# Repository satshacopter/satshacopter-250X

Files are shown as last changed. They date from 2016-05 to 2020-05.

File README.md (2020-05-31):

<h1 style="font-family: courier;" align="center">satshacopter 250X</h1>
<p align="center">
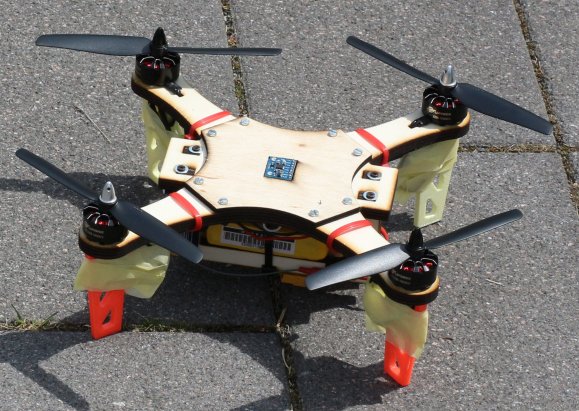
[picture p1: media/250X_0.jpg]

<div align="center"><i>An open source, low cost and fabbable quad X drone.</i></div>
</p>  

satshacopter 250X
--

satshacopter 250X is a quadcopter built around the **[satshakit flight controller](https://github.com/satshakit/satshakit-flight-controller)**. It is designed to be **simple and cheap as much as possible**, and to be easily made inside any **Fab Lab**.

250X specifications:

- **250mm wood frame** and supports
- **open source flight controller**
- **MPU6050 IMU** located exactly at the center
- 4 x 1900kv **brushless motors**
- 4 x 15A **ESCs**
- **MultiWii** compatible
- Hobby King 4 channel **remote and receiver**
- 1000mah 3S **LiPo battery** 
- costs under **100€**

Here you can look about the **MultiWii pin mapping** of the satshakit flight controller board:

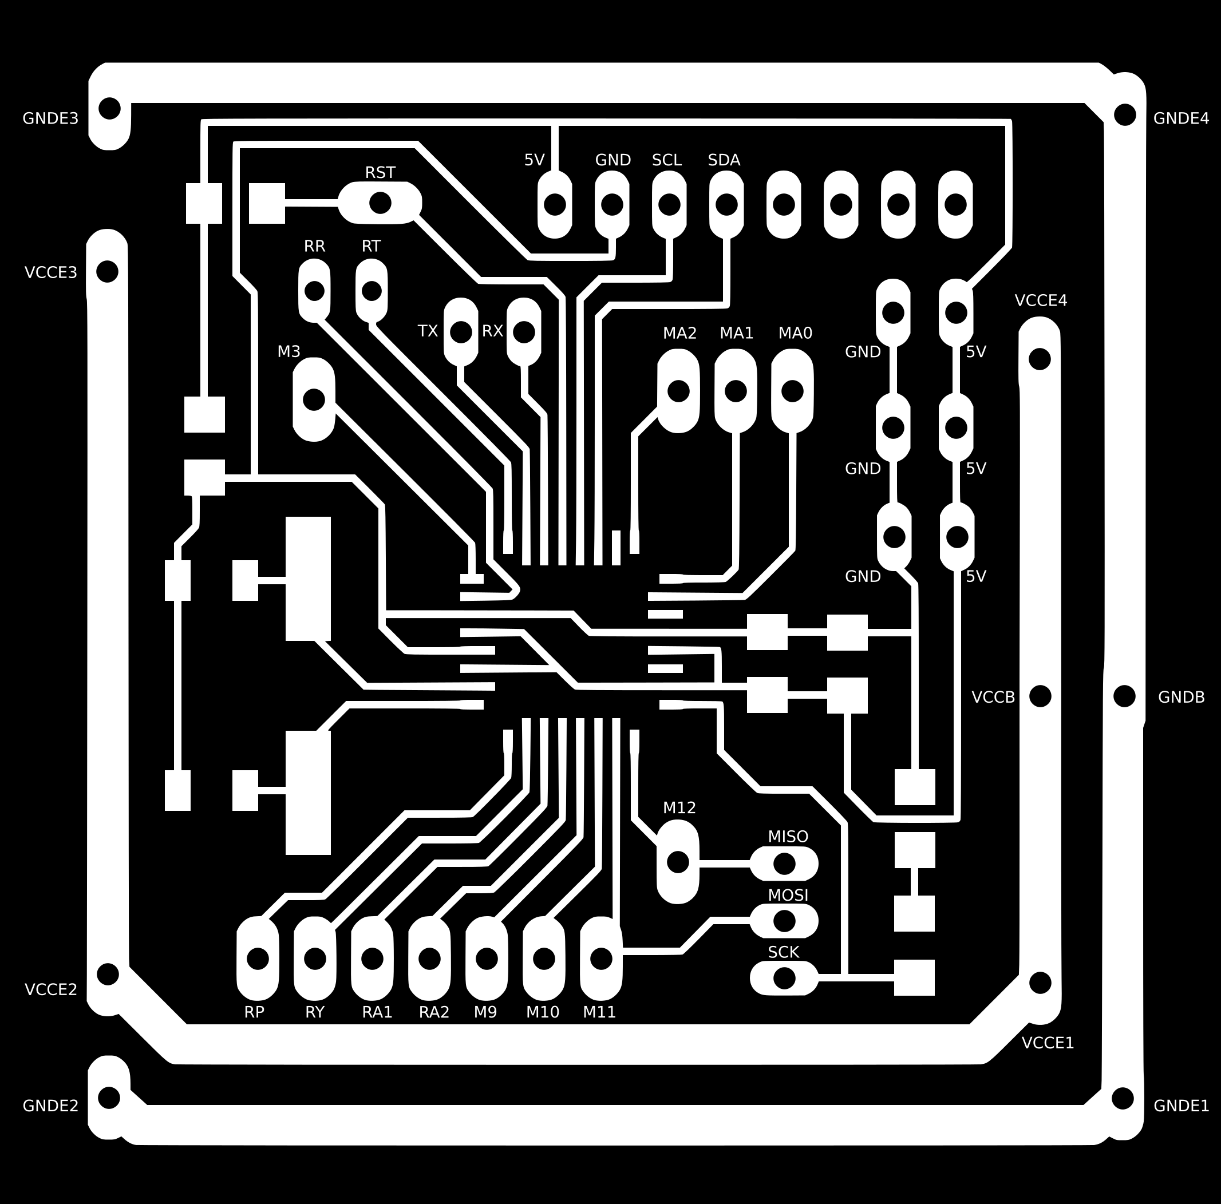
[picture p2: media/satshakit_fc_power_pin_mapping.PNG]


And here you can che the required components in the **Bill of Material** table:

|name|description|vendor|link|price|notes|
|:---:| :---:|:---:|:---:|:---:|:---:|
|2.4Ghz4Ch TxRx V2|4ch mode 2 remote control and receiver|Hobby King|[link](http://www.hobbyking.com/hobbyking/store/__66499__Hobby_King_2_4Ghz_4Ch_Tx_Rx_V2_Mode_2_EU_Warehouse_.html)|23.14€|-|
|Zippy Compact|battery 1000mah 3s|Hobby King|[link](http://www.hobbyking.com/hobbyking/store/__36064__ZIPPY_Compact_1000mAh_3S_25C_Lipo_Pack_EU_Warehouse_.html)|5.55€|-|
|LDPOWER D250-2 Multicopter Power System|4 x 2206-1900kv motors and 4 x 15A ESC|Hobby King EU|[link](http://www.hobbyking.com/hobbyking/store/__84723__LDPOWER_D250_2_Multicopter_Power_System_2206_1900kv_6_x_3_4_Pack_EU_Warehouse_.html)|43.81€|propellers Included|
|IMU 6DOF|MPU6050 Gyro + Acc IMU|Ebay|[link](http://www.ebay.de/itm/MPU-6050-GY-521-3-Achsen-Gyroskop-Accelerometer-Kreisel-Board-Sensor-Arduino-21-/121887579651)|5.39€|-|
|LiPo Charger and Balancer|800mah 3s LiPo charger|Hobby King|[link](http://www.hobbyking.com/hobbyking/store/uh_viewitem.asp?idproduct=77525)|6.99€|-|
|Fligh Controller|satshakit flight controller|various|[link](https://github.com/satshakit/satshakit-flight-controller)|4.00-8.00€|depending on the quantity|
|Voltage regulator|Pololu step up step down 5V S7V7F5|E-shop|[link](https://www.flikto.de/products/pololu-5v-step-up-step-down-voltage-regulator-s7vf5)|4.31€|-|
||||**Total price**|89.19€+4/8€|-|

NOTE: prices may change over time on the respective vendors, and also it is highly dependand on the quantity of drones you want to make.

Downloads
--

If you want to build by yourself a satshacopter 250X, please download the detailed **build manual** here:

- [satshacopter 250X detailed build manual](https://github.com/satshacopter/satshacopter-250X/raw/master/docs/250X/satshacopter-250x-building-manual.pdf)

Following you can find all the **design files** you need to make it:

- [satshakit flight controller eagle board](https://raw.githubusercontent.com/satshacopter/satshacopter-250X/master/eagle_projects/satshakit_flight_controller/satshakit_fc_power.brd)
- [satshakit flight controller eagle sch](https://raw.githubusercontent.com/satshacopter/satshacopter-250X/master/eagle_projects/satshakit_flight_controller/satshakit_fc_power.sch)
- [satshakit flight controller internal traces png](https://raw.githubusercontent.com/satshacopter/satshacopter-250X/master/media/satshakit_fc_power_internal.png)
- [satshakit flight controller holes png](https://raw.githubusercontent.com/satshacopter/satshacopter-250X/master/media/satshakit_fc_power_holes.png)
- [satshakit flight controller cut png](https://raw.githubusercontent.com/satshacopter/satshacopter-250X/master/media/satshakit_fc_power_cut.png)
- [main frame and supports Rhino](https://github.com/satshacopter/satshacopter-250X/raw/master/design_files/main_frame_and_supports_8mm.3dm)
- [main frame and supports dxf](https://github.com/satshacopter/satshacopter-250X/raw/master/design_files/main_frame_and_supports_8mm.dxf)
- [upper frame and supports Rhino](https://github.com/satshacopter/satshacopter-250X/raw/master/design_files/upper_frame_4mm.3dm)
- [upper frame and supports dxf](https://raw.githubusercontent.com/satshacopter/satshacopter-250X/master/design_files/upper_frame_4mm.dxf)
- [foot Rhino](https://github.com/satshacopter/satshacopter-250X/raw/master/design_files/foot.3dm)
- [foot stl](https://github.com/satshacopter/satshacopter-250X/raw/master/design_files/foot.stl)
- [satshacopter 250X detailed BOM Excel](https://github.com/satshacopter/satshacopter-250X/raw/master/docs/250X/250X_BOM.xlsx)
- [satshacopter 250X detailed BOM Open document](https://github.com/satshacopter/satshacopter-250X/raw/master/docs/250X/250_BOM.ods)

Media
--

Some images of a built satshacopter 250X

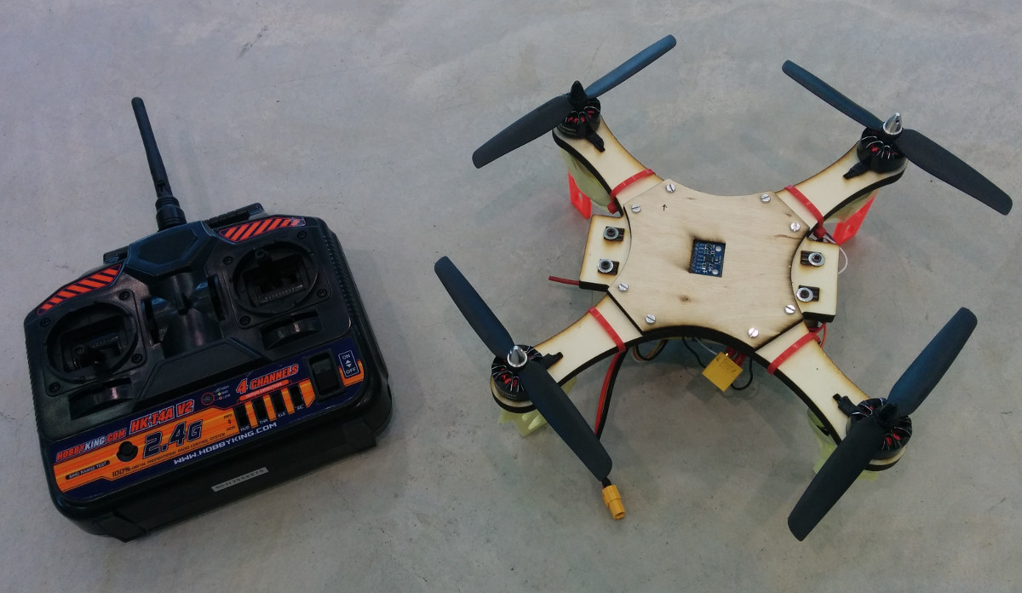
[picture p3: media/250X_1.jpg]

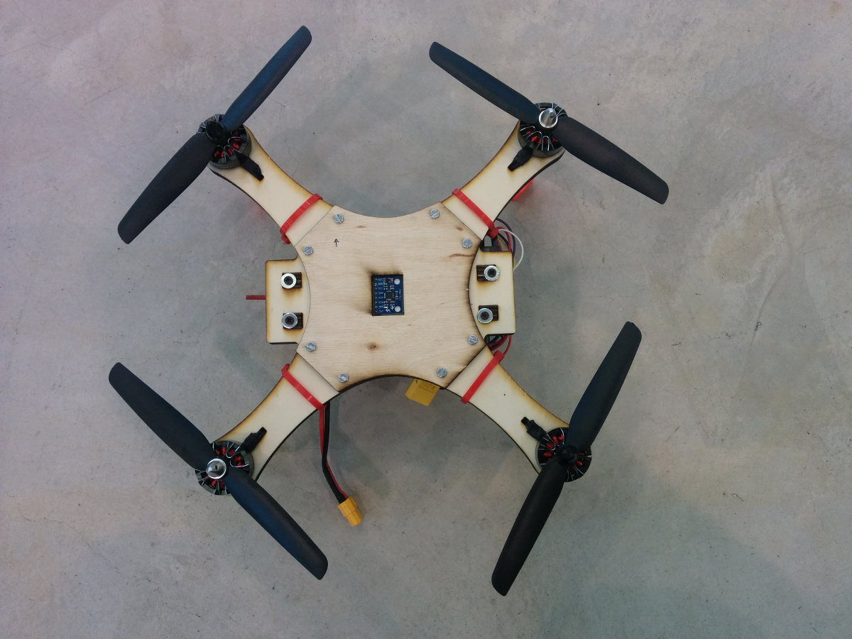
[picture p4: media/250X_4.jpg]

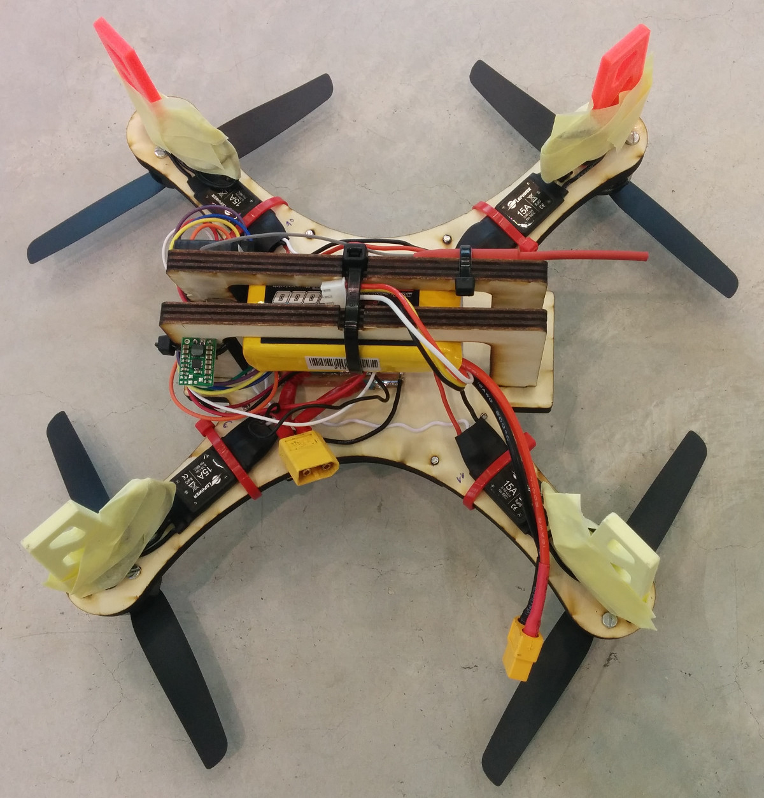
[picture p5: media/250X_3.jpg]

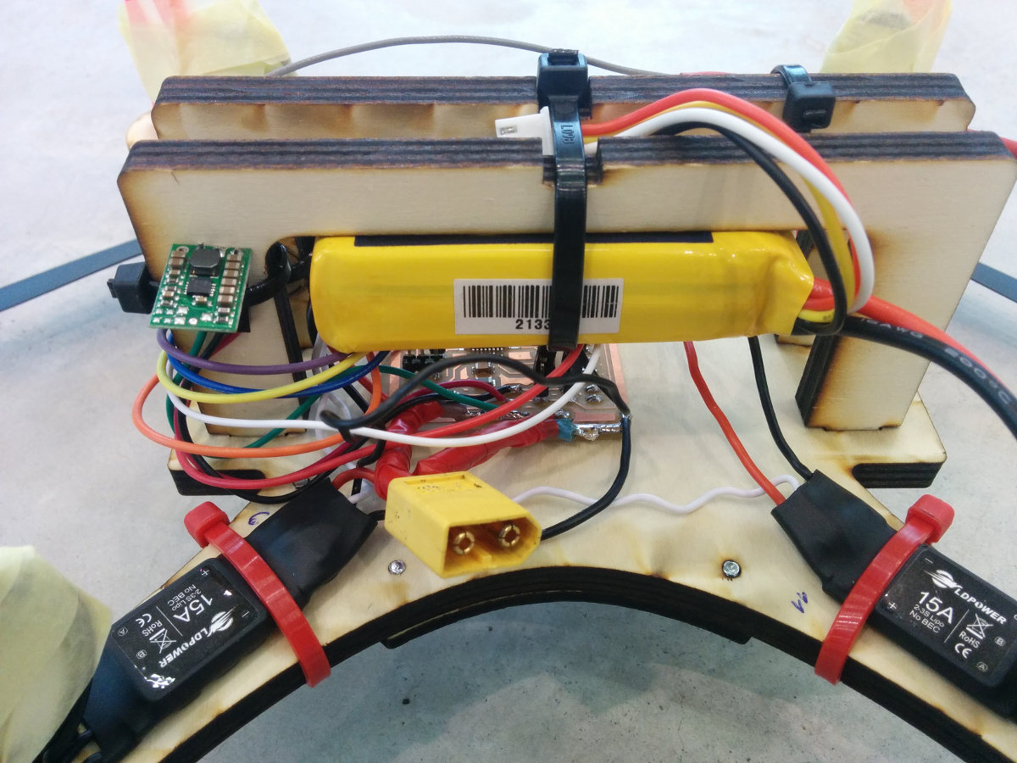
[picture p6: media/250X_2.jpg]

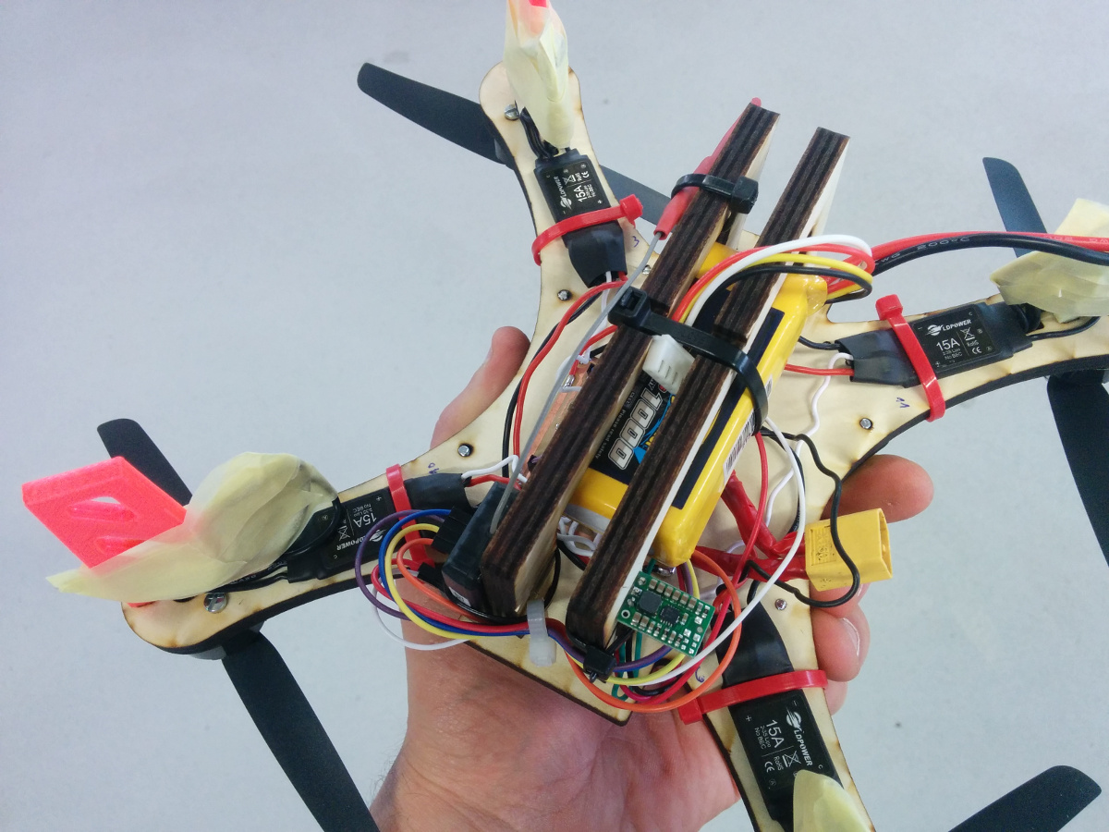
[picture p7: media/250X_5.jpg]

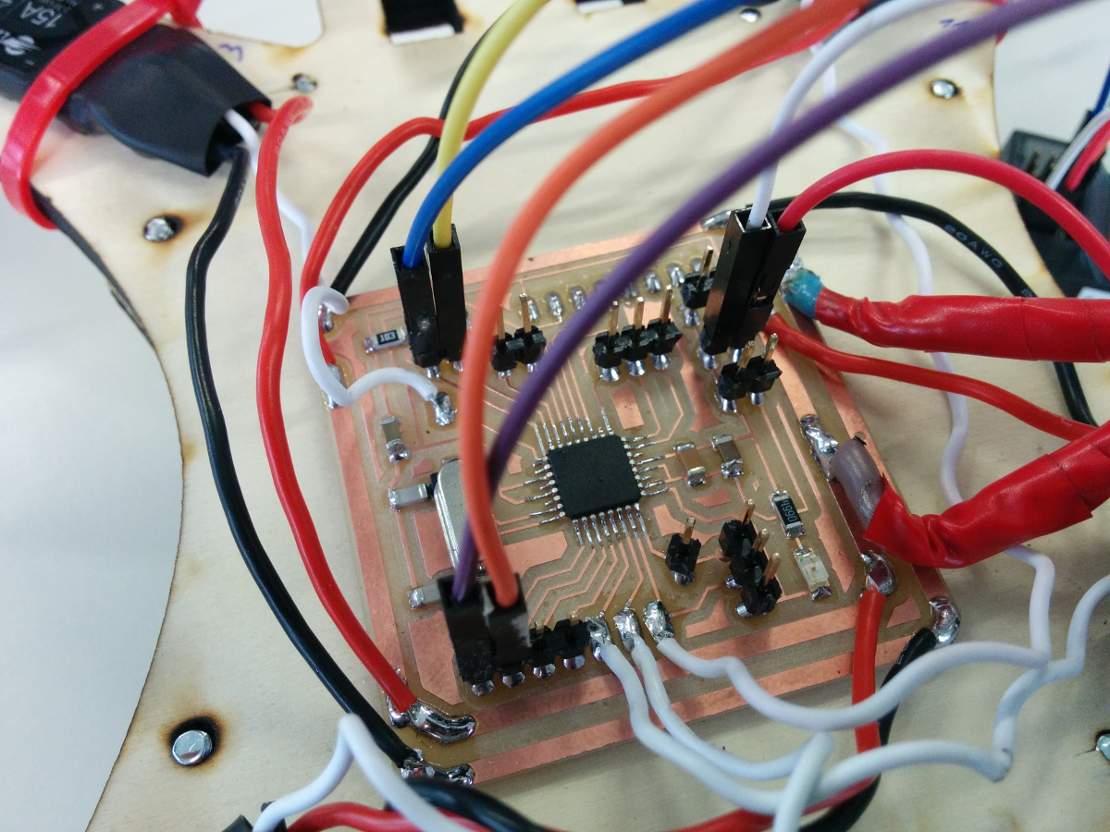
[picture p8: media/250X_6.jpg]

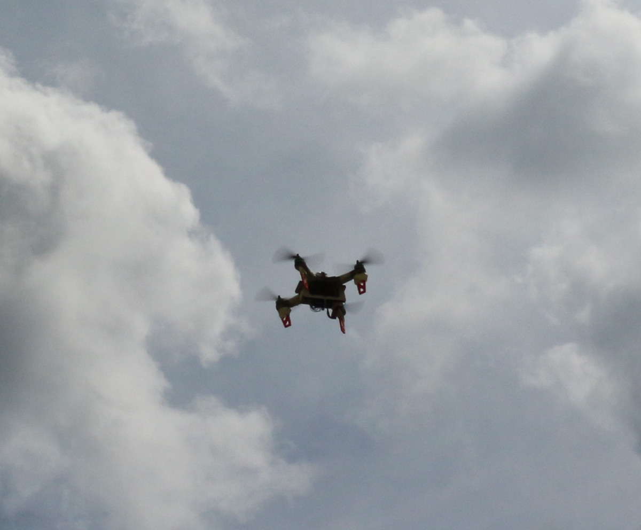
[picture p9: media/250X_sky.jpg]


satshacopter 250X perfomance test:

<a href="http://www.youtube.com/watch?feature=player_embedded&v=MrtPuotW08c
" target="_blank"></a>

Safety
--

Please try always to fly safe.

Here are my personal safety recommendations, especially for experimental drones of which you are not sure on how they can behave:

- make sure to always keep an HUGE distance between you and the drone
- always place yourself on the back of the drone before starting flying
- always have the direct sight to the drone and make sure that its orientation is clear for you (use different colors or LEDs)
- fly in private areas where no public can access
- make sure that nobody can come near the drone while you are flying
- make sure that you cannot destroy anything that you have around you with the drone
- check the wind and the weather before flying, if outdoor
- never go too high (no more than 1/2 meters in these cases)
- do not fly on top of someone (neither yourself)
- first try to fly few cm above the ground to see if everything is correct
- try to avoid using carbon fiber props (they are really like rotating knifes) but use plastic props
- try to use smaller drones with smaller props for really experimental tests
- triple check all the screws and that the frame is not cracked somewhere
- triple check all the DIY electronics, if it fails in-flight can be extremely dangerous
- make sure that the batteries are full charged (both transmitter and the LiPos)

Authors
--

- Daniele Ingrassia

Contact
--

- **ingrassiada@gmail.com**
- **[linkedin](http://it.linkedin.com/in/danieleingrassia)**

Thanks
--

[Fablab Kamp-Lintfort](http://fablab.hochschule-rhein-waal.de/index.php/de/)<br />
Hochschule Rhein-Waal<br />
Friedrich-Heinrich-Allee 25, 47475 Kamp-Lintfort, Germany<br />
fablab@hochschule-rhein-waal.de

License
--
This work is licensed under the terms of the open source license: Creative Commons Attribution-ShareAlike 4.0 International ([CC BY-SA 4.0](https://creativecommons.org/licenses/by-sa/4.0/)).

Disclaimer  
--

<div class="align-justify">
This hardware/software is provided "as is", and you use the hardware/software at your own risk. Under no circumstances shall any author be liable for direct, indirect, special, incidental, or consequential damages resulting from the use, misuse, or inability to use this hardware/software, even if the authors have been advised of the possibility of such damages.</div>

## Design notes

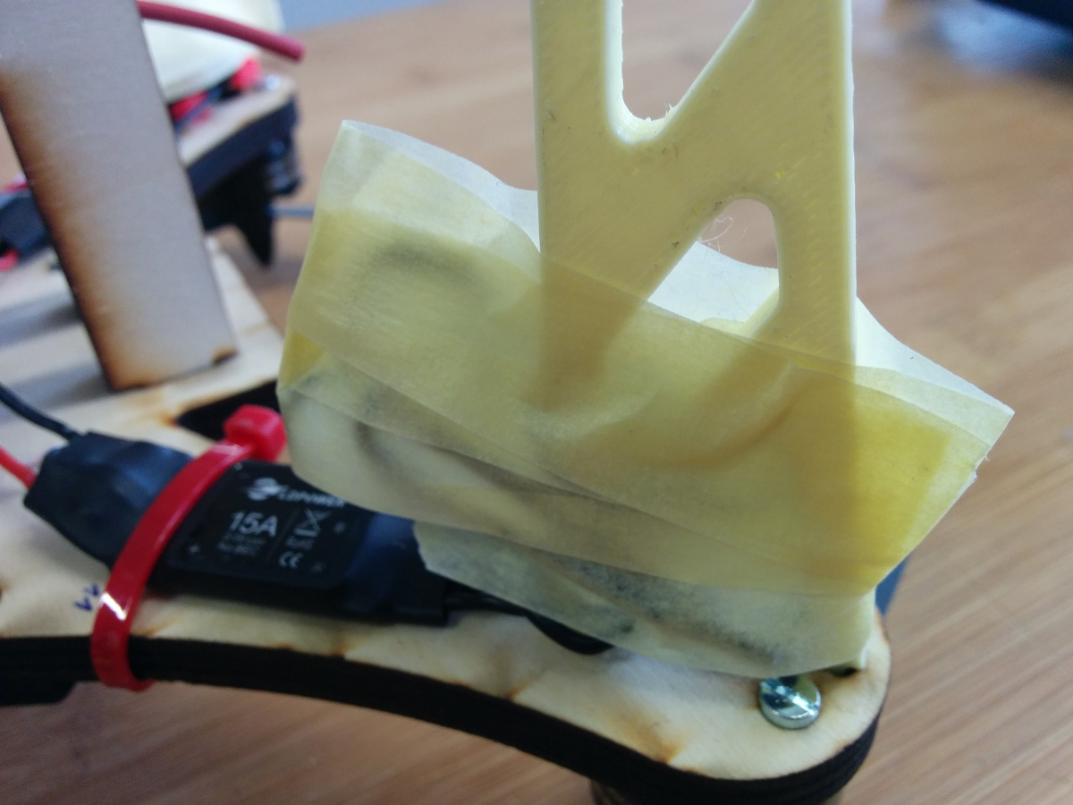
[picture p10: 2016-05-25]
media/scotch_tape_motors.jpg

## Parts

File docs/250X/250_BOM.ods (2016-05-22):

Name | Description | Vendor | Link | Unit Price | Total price x 5 | Notes
2.4Ghz4Ch TxRx V2 | 4ch mode 2 remote control and receiver | Hobby King EU | link (http://www.hobbyking.com/hobbyking/store/__66499__Hobby_King_2_4Ghz_4Ch_Tx_Rx_V2_Mode_2_EU_Warehouse_.html) | 23.14 | 115.70 | -
Zippy Compact | battery 1000mah 3s | Hobby King EU | link (http://www.hobbyking.com/hobbyking/store/__36064__ZIPPY_Compact_1000mAh_3S_25C_Lipo_Pack_EU_Warehouse_.html) | 5.55 | 27.75 | -
LDPOWER D250-2 Multicopter Power System | 4 x 2206-1900kv motors and 4 x 15A esc | Hobby King EU | link (http://www.hobbyking.com/hobbyking/store/__84723__LDPOWER_D250_2_Multicopter_Power_System_2206_1900kv_6_x_3_4_Pack_EU_Warehouse_.html) | 43.81 | 219.05 | Propellers Included
IMU 6DOF | MPU6050 Gyro + Acc IMU | Ebay (local) | link (http://www.ebay.de/itm/MPU-6050-GY-521-3-Achsen-Gyroskop-Accelerometer-Kreisel-Board-Sensor-Arduino-21-/121887579651) | 5.39 | 26.95 | Local (near Rheinberg)
LiPo Charger and Balancer | 800mah 3s LiPo charger | Hobby King EU | link (http://www.hobbyking.com/hobbyking/store/uh_viewitem.asp?idproduct=77525) | 6.99 | 34.95
Frame | 8mm + 2mm plywood frame | Local | - | 2.00 | 10.00 | -
Fligh Controller | satshakit flight controller | Various | - | 4.00 | 20.00
Copper sheet | FR4 80 x 160 | Various | - | 1.00 | 5.00 | A lot of spare space for mistakes in engraving
Battery connectors | XT 60 female connectors | Hobby King EU | link (http://www.hobbyking.com/hobbyking/store/__36304__Female_XT60_Connectors_5pcs_bag_GENUINE_EU_Warehouse_.html) | 0.58 | 2.90 | already x 5
Motor And Frame Screws | M3 10 x 8 + M3 12 x 4 + nuts and washers | Local | - | 0.50 | 2.50 | -
AA Batteries for the remote | 8 x AA 1.5V batteries | Local | - | 1.60 | 8.00 | -
Voltage regulator 5V | S7V7F5 | E-shop | link (https://www.flikto.de/products/pololu-5v-step-up-step-down-voltage-regulator-s7vf5) | 4.31 | 21.55
 |  |  |  | Shipping of all: | 9.00 | 7€ combined Hobby King + 2€ E-shop
 |  |  |  | Price singe drone without shipping | Price 5 drones incl. shipping
 |  |  |  | 98.87 | 503.35

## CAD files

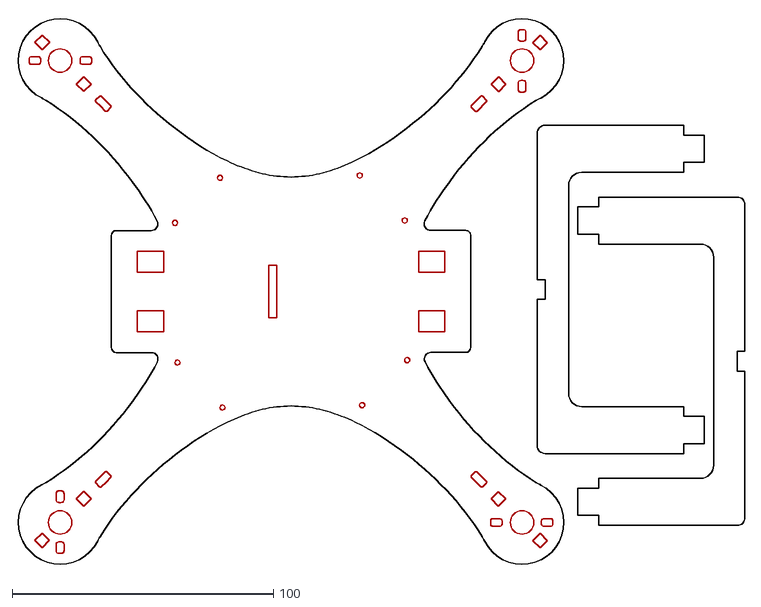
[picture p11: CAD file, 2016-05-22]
design_files/main_frame_and_supports_8mm.dxf
279.0 x 210.5

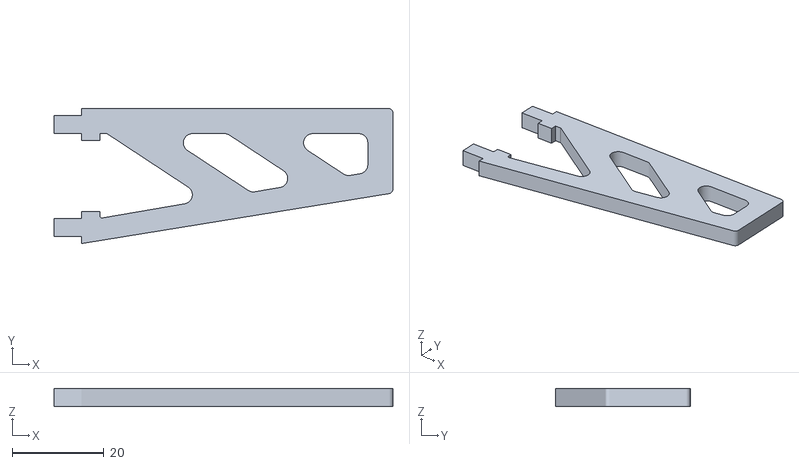
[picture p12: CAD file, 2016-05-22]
design_files/foot.stl
74.0 x 29.5 x 4.00

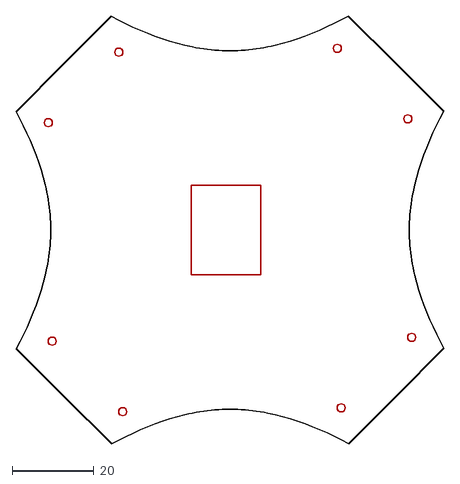
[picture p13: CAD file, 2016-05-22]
design_files/upper_frame_4mm.dxf
104.7 x 104.7

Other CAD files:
design_files/foot.3dm
design_files/main_frame_and_supports_8mm.3dm
design_files/upper_frame_4mm.3dm

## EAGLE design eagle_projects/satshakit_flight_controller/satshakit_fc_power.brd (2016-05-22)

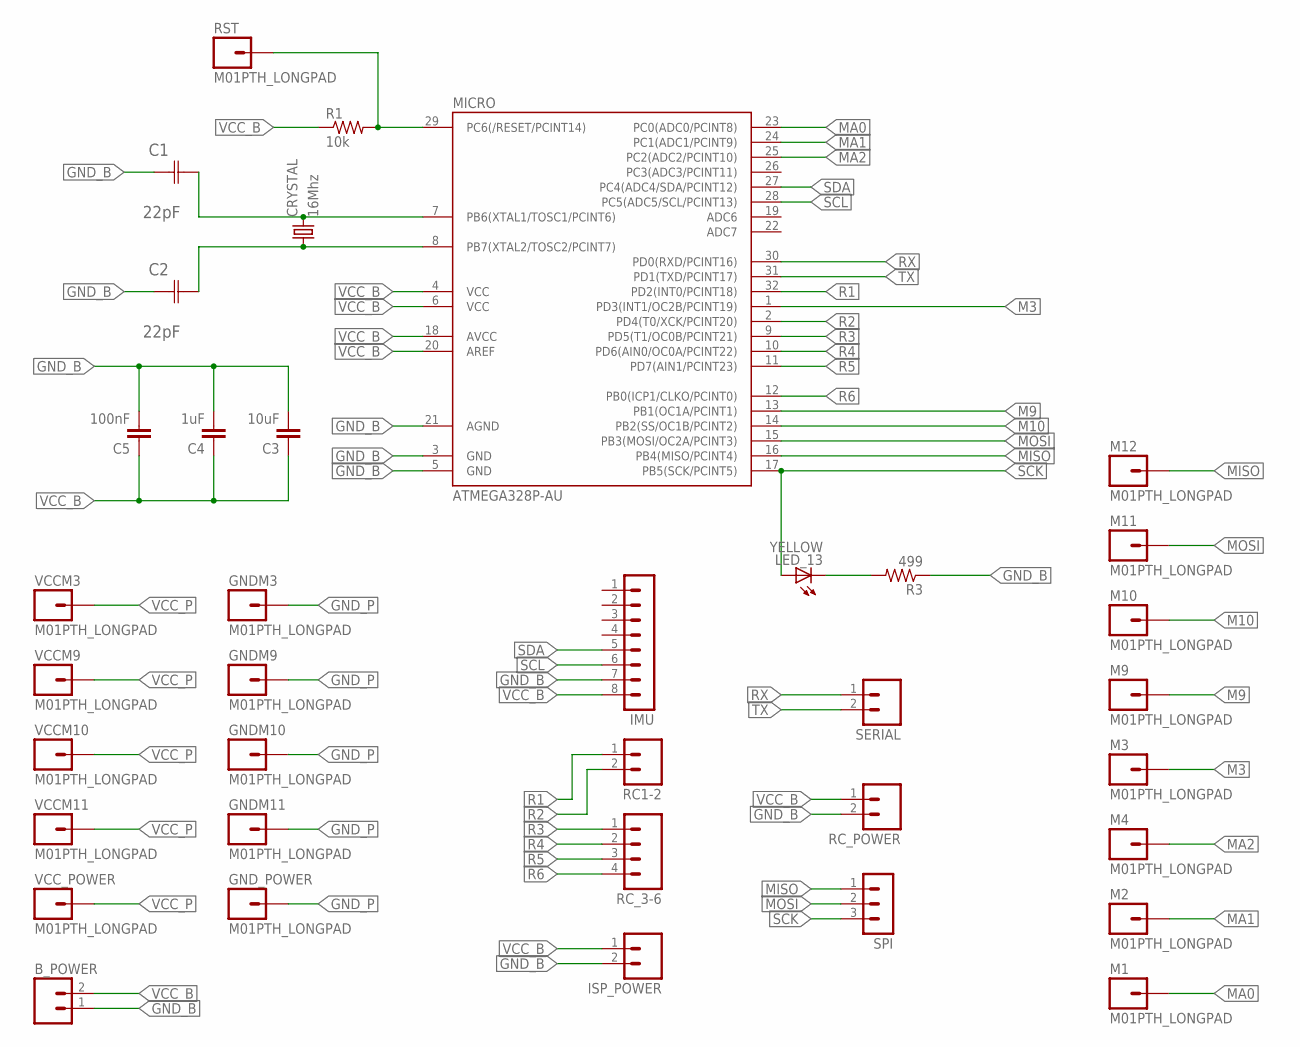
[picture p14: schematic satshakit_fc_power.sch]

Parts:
B_POWER: M02LOCK_LONGPADS; 1X02_LOCK_LONGPADS
C1, C2: 22pF; CAPC3216X178N
C3: 10uF; 1206
C4: 1uF; 1206
C5: 100nF; 1206
CRYSTAL: 16Mhz; CSM-7X-DU
GNDM3, GNDM9, GNDM10, GNDM11: M01PTH_LONGPAD; 1X01_LONGPAD
GND_POWER: M01PTH_LONGPAD; 1X01_LONGPAD
IMU: MA08-1
ISP_POWER: M02LOCK_LONGPADS; 1X02_LOCK_LONGPADS
LED_13: YELLOW; 1206
M1, M2, M3, M4, M9, M10, M11, M12: M01PTH_LONGPAD; 1X01_LONGPAD
MICRO: ATMEGA328P-AU; TQFP32-08
R1: 10k; 1206
R3: 499; 1206
RC1-2: M02; 02P
RC_3-6: M04LONGPADS; 1X04_LONGPADS
RC_POWER: M02LOCK_LONGPADS; 1X02_LOCK_LONGPADS
RST: M01PTH_LONGPAD; 1X01_LONGPAD
SERIAL: M02LOCK_LONGPADS; 1X02_LOCK_LONGPADS
SPI: MA03-1
VCCM3, VCCM9, VCCM10, VCCM11: M01PTH_LONGPAD; 1X01_LONGPAD
VCC_POWER: M01PTH_LONGPAD; 1X01_LONGPAD

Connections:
GND_B: B_POWER.1, C1.1 (C1), C2.1 (C1), C3.2, C4.2, C5.2, IMU.7, ISP_POWER.2, MICRO.3 (GND), MICRO.5 (GND), MICRO.21 (AGND), R3.1, RC_POWER.2
GND_P: GNDM3.1, GNDM9.1, GNDM10.1, GNDM11.1, GND_POWER.1
M3: M3.1, MICRO.1 (PD3(INT1/OC2B/PCINT19))
M9: M9.1, MICRO.13 (PB1(OC1A/PCINT1))
M10: M10.1, MICRO.14 (PB2(SS/OC1B/PCINT2))
MA0: M1.1, MICRO.23 (PC0(ADC0/PCINT8))
MA1: M2.1, MICRO.24 (PC1(ADC1/PCINT9))
MA2: M4.1, MICRO.25 (PC2(ADC2/PCINT10))
MISO: M12.1, MICRO.16 (PB4(MISO/PCINT4)), SPI.1
MOSI: M11.1, MICRO.15 (PB3(MOSI/OC2A/PCINT3)), SPI.2
unnamed: C1.2 (C2), CRYSTAL.2, MICRO.7 (PB6(XTAL1/TOSC1/PCINT6))
unnamed: MICRO.29 (PC6(/RESET/PCINT14)), R1.2, RST.1
unnamed: C2.2 (C2), CRYSTAL.1, MICRO.8 (PB7(XTAL2/TOSC2/PCINT7))
unnamed: LED_13.2 (C), R3.2
R1: MICRO.32 (PD2(INT0/PCINT18)), RC1-2.1
R2: MICRO.2 (PD4(T0/XCK/PCINT20)), RC1-2.2
R3: MICRO.9 (PD5(T1/OC0B/PCINT21)), RC_3-6.1
R4: MICRO.10 (PD6(AIN0/OC0A/PCINT22)), RC_3-6.2
R5: MICRO.11 (PD7(AIN1/PCINT23)), RC_3-6.3
R6: MICRO.12 (PB0(ICP1/CLKO/PCINT0)), RC_3-6.4
RX: MICRO.30 (PD0(RXD/PCINT16)), SERIAL.1
SCK: LED_13.1 (A), MICRO.17 (PB5(SCK/PCINT5)), SPI.3
SCL: IMU.6, MICRO.28 (PC5(ADC5/SCL/PCINT13))
SDA: IMU.5, MICRO.27 (PC4(ADC4/SDA/PCINT12))
TX: MICRO.31 (PD1(TXD/PCINT17)), SERIAL.2
VCC_B: B_POWER.2, C3.1, C4.1, C5.1, IMU.8, ISP_POWER.1, MICRO.4 (VCC), MICRO.6 (VCC), MICRO.18 (AVCC), MICRO.20 (AREF), R1.1, RC_POWER.1
VCC_P: VCCM3.1, VCCM9.1, VCCM10.1, VCCM11.1, VCC_POWER.1

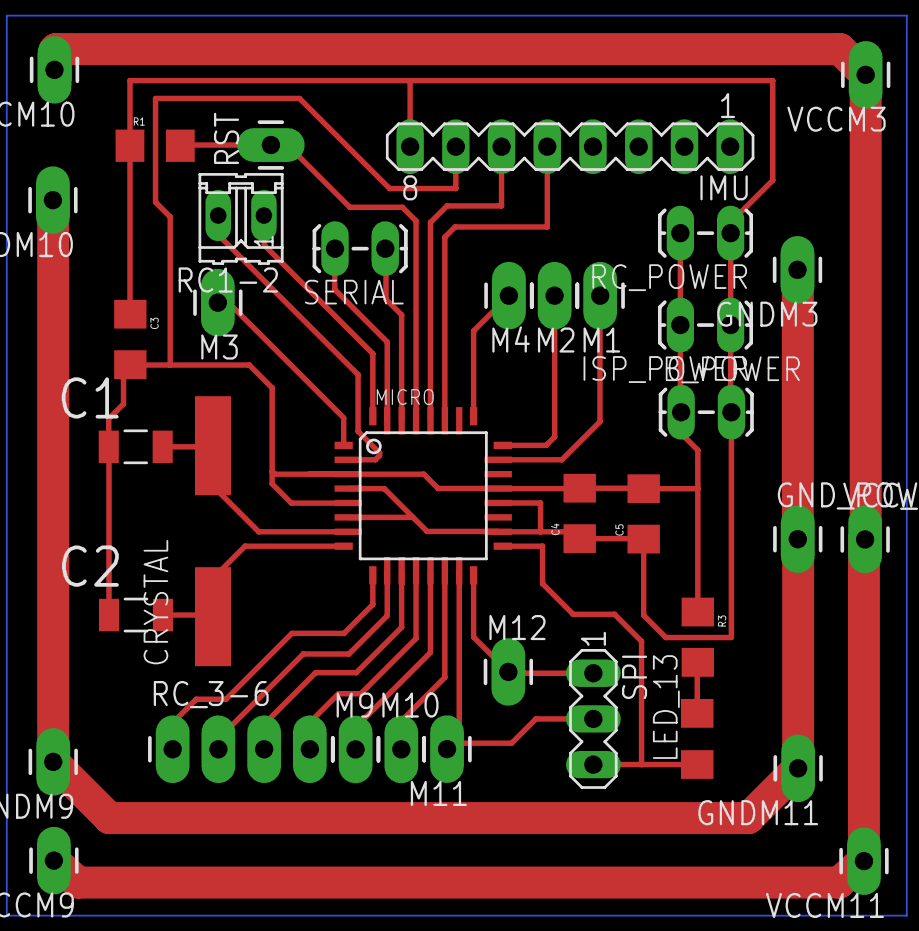
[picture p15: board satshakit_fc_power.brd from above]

Board: 2 copper layers, 37 parts (0 on the bottom side), 27 nets.

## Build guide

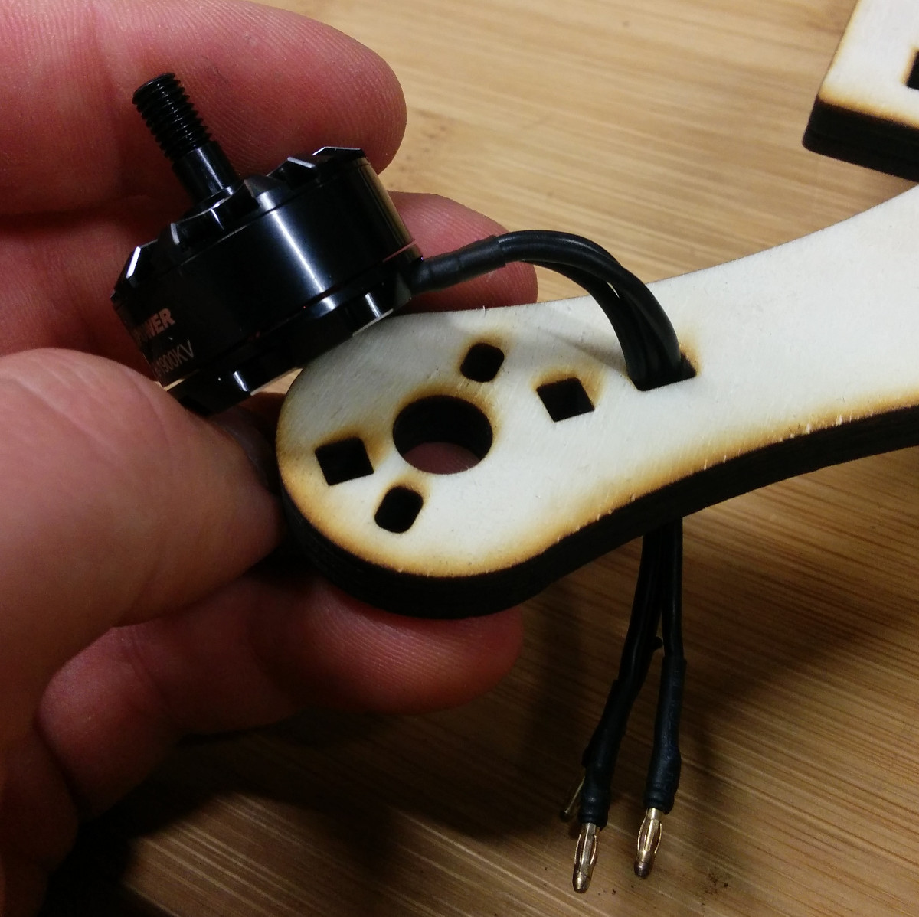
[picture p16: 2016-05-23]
media/motor_assembly_1.jpg

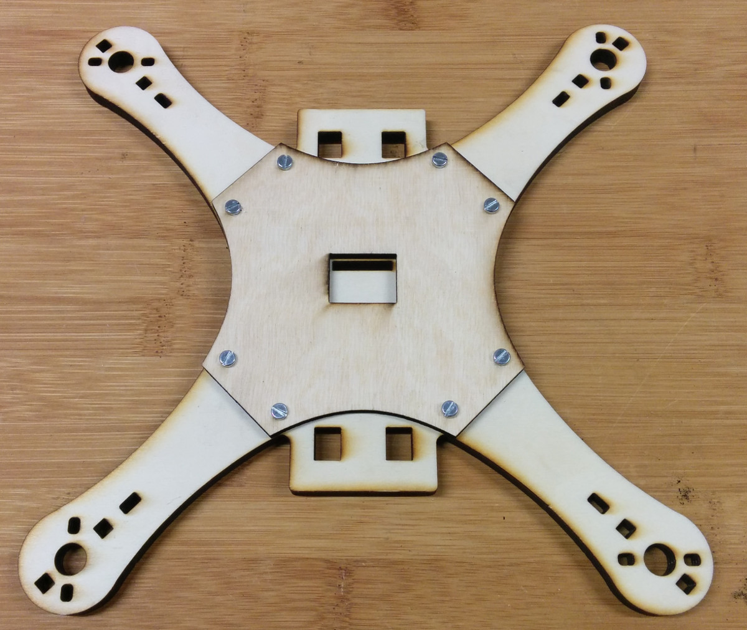
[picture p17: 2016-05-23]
media/frame_assembly_3.jpg

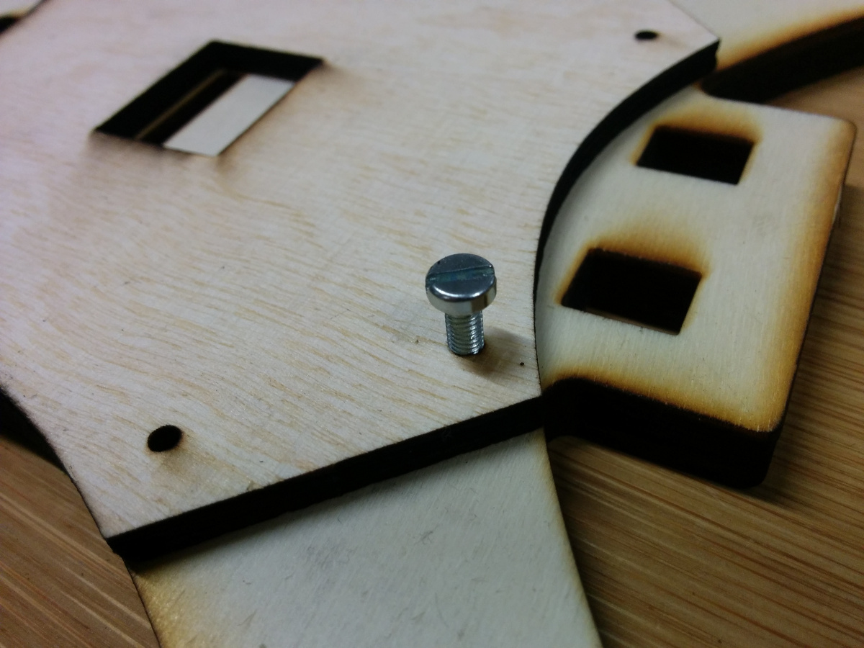
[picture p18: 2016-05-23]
media/frame_Assembly_2.jpg

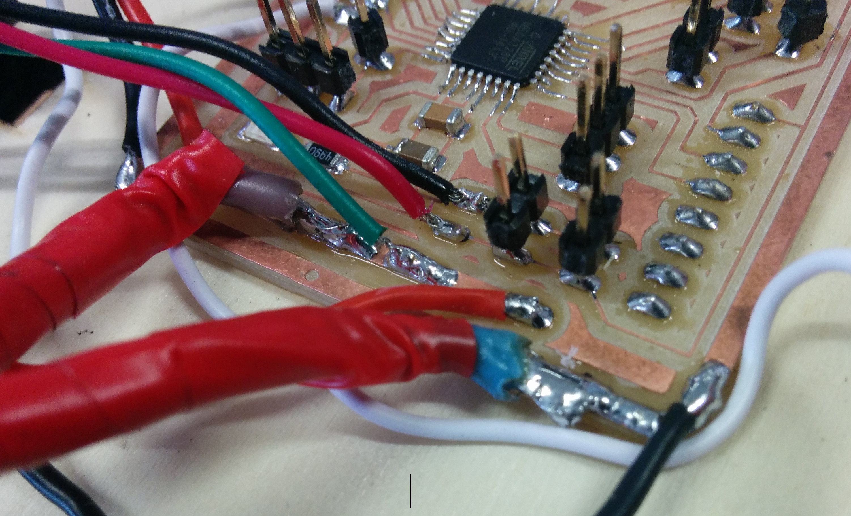
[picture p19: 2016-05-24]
media/strong_soldering.jpg

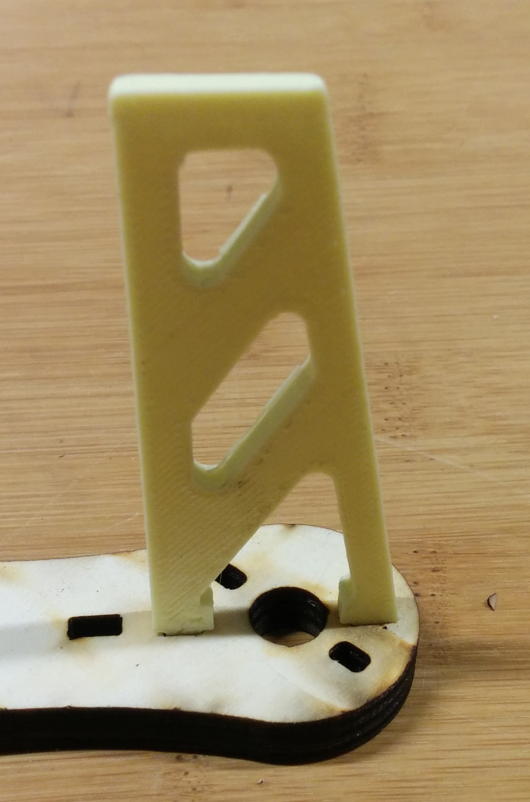
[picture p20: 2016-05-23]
media/foots_assembly_2.jpg

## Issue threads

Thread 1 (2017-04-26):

Firmware Installation and default baud rate

jsphpl, 2017-04-26:
Hey Daniele, it seems like i can't find any instructions on the firmware installation. I assume all that needs to be done is to install [MultiWii](https://github.com/multiwii/multiwii-firmware) - can you provide a working default configuration for satshacopter please?

I am currently trying to get the copter here at Erfindergarden working. For this purpose, i'd like to connect using [Baseflight Configurator](https://chrome.google.com/webstore/detail/baseflight-configurator/mppkgnedeapfejgfimkdoninnofofigk?hl=en) or at least some serial terminal. Just to be sure: the boards that you made – at which baud rate are they communicating on the FTDI?

Thank you and best wishes from munich!
Joseph

satshas, 2017-04-26:
Hi Joseph,

I suppose that you are trying to make the quadcopter work, but maybe you did not read the README of the repo which contains the link to the building manual?

Other than the main page you can find it in the following link, which is actually inside the repo if you make a clone:
https://github.com/satshacopter/satshacopter-250X/raw/master/docs/250X/satshacopter-250x-building-manual.pdf

On this manual, starting from page 25, you'll find the instructions on how to configure the config.h and upload the Multiwii.ino.

For the calibration you can use the Multiwii GUI, and the procedure is described  starting from page 48.

I never tried Baseflight and its GUI so I cannot help you on this, also because the drone was not intended to work with it, but maybe it can.

Let me know if the manual is enough or you need any other information ;)

Cheers from Kamp-Lintfort,
Daniele

jsphpl, 2017-04-27:
Well the readme i read, of course. But i must admit i've been too lazy to read the entire build manual… Thanks for the hint! I'll let you know how it works out…

Closed 2017-04-26.

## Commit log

2016-05-22 first commit of satshacopter
    [250X_DOM.xlsx, 250_BOM.ods, foot.3dm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]
2016-05-22 changed BOM
    [250X_DOM.xlsx, 250_BOM.ods]
2016-06-30 changed design file name
    [main_frame_and_supports_8mm.dxf]
2017-01-22 fixed bom file name
    [250X_BOM.xlsx]

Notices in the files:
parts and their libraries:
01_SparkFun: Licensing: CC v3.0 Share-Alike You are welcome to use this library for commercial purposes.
